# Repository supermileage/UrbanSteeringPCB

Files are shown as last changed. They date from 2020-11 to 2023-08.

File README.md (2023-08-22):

# Urban Steering PCB

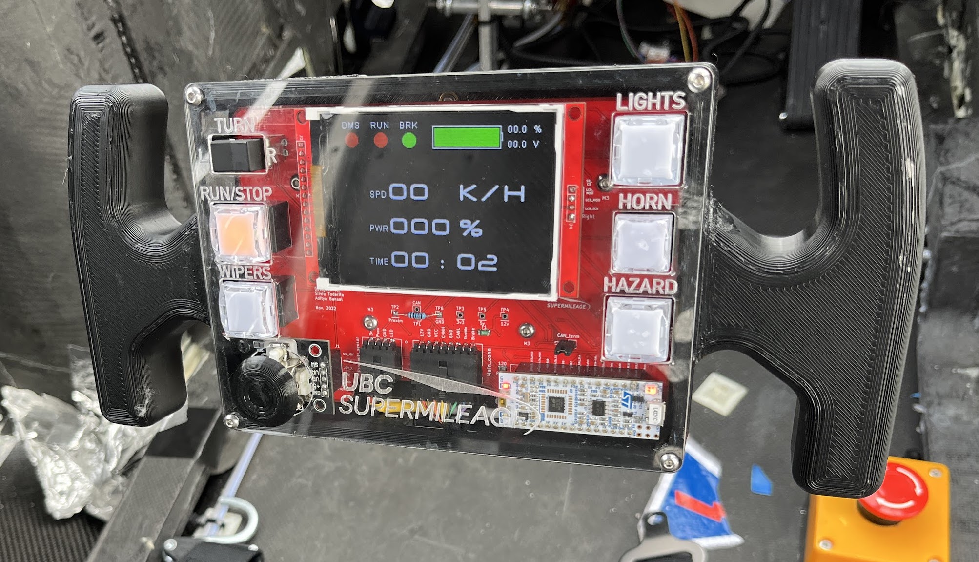
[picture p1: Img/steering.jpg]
Urban Steering Wheel


The steering wheel for the UBC Supermileage Urban Concept electric vehicle is designed to steer the vehicle, provide information to the driver, and allow the driver to control the vehicle. This repo contains the design files for the printed circuit board at the core of the steering wheel. 

Some features of this PCB:

- STM32L432 Microcontroller with built-in CAN controller
- MCP 2562 CAN Transceiver
- 74HC595 and 74HC597 shift registers for LED output & button input
- ILI9341 3.2" LCD Screen
- Mechanical buttons with dual-color LEDs
- IR proximity sensor for dead man's switch functionality
- SD Card Reader
- Joystick

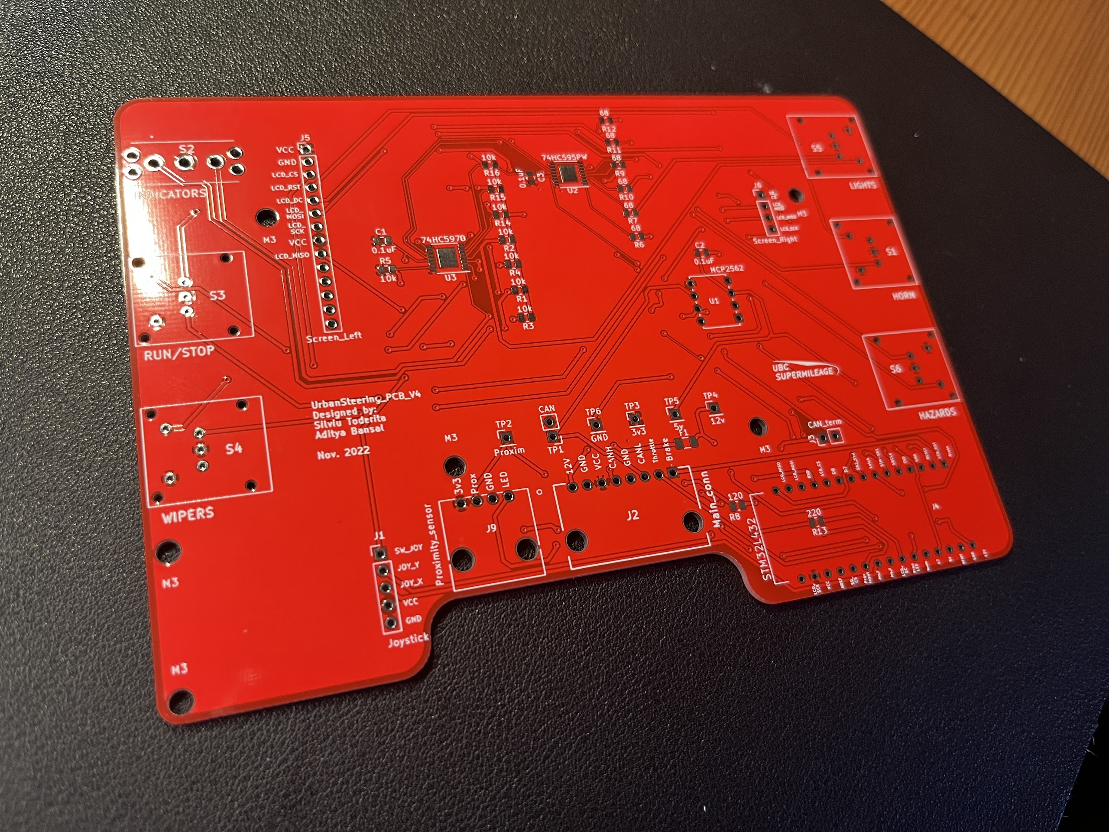
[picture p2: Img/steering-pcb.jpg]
Urban Steering PCB


## Schematic

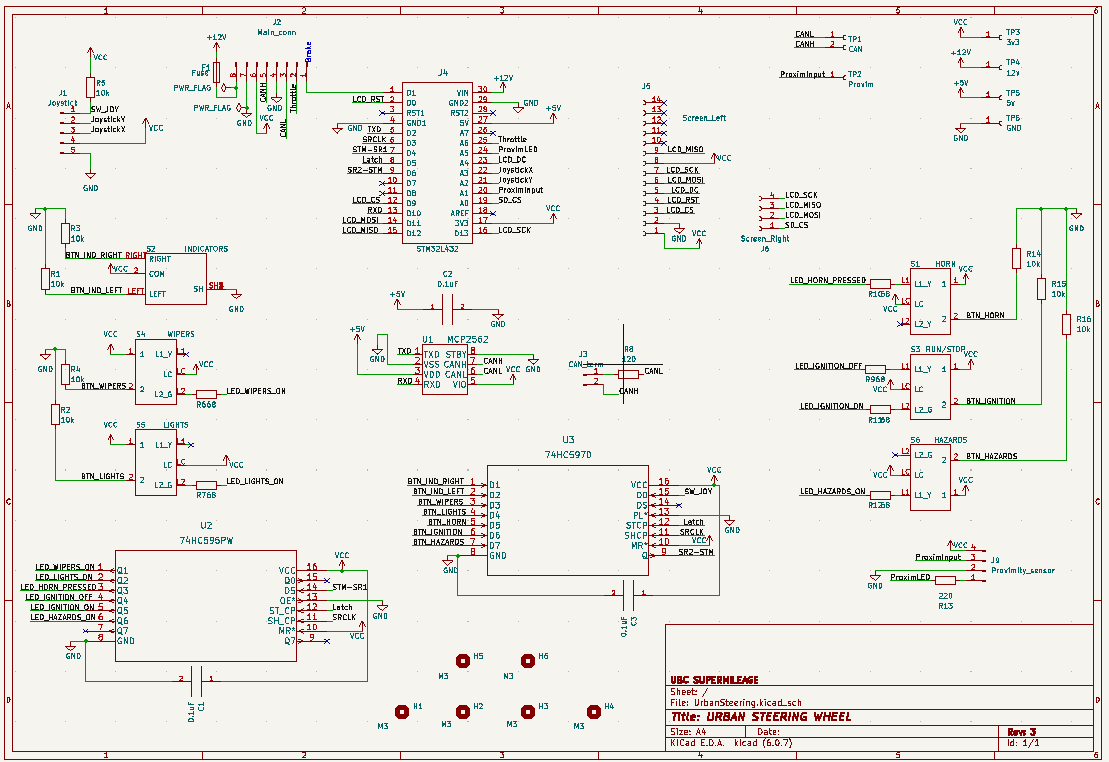
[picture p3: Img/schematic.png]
Schematic Diagram


## Layout 

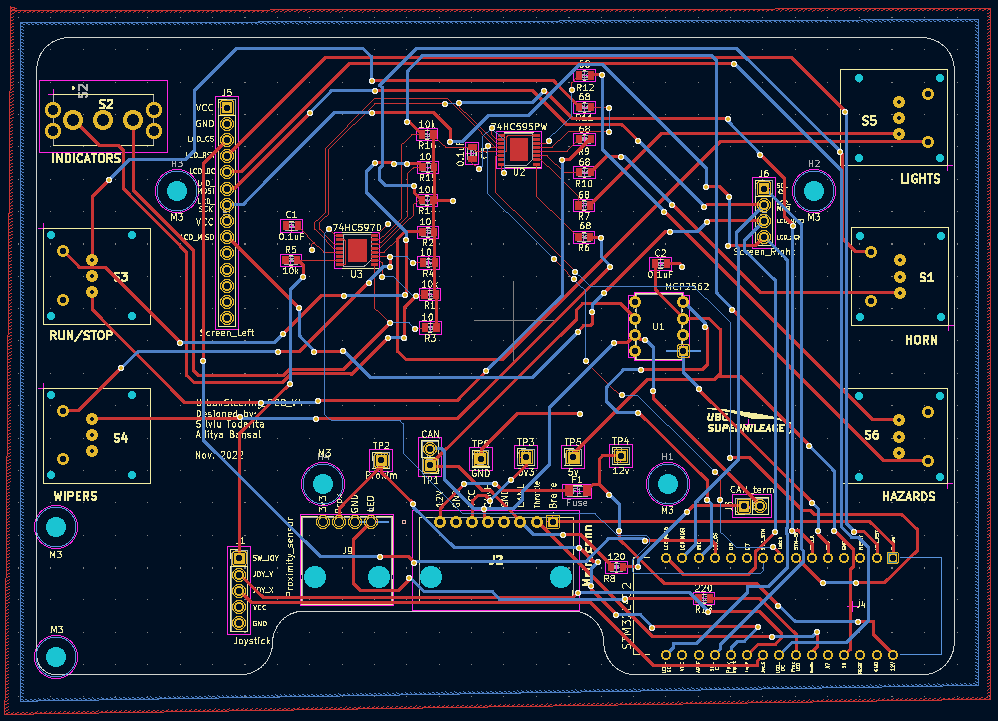
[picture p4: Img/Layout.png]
Unfilled Layout


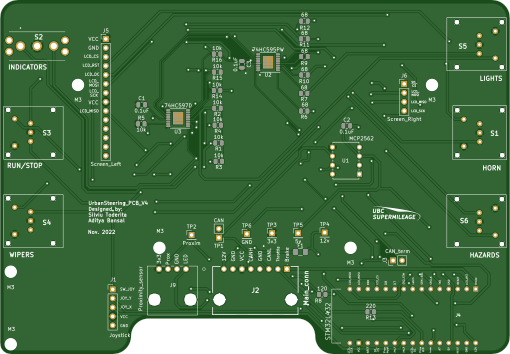
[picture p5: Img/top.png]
Front Render


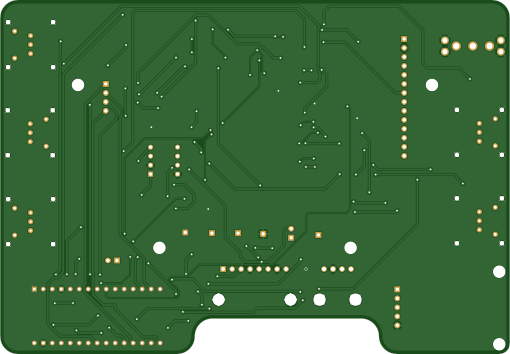
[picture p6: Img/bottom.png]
Back Render


## Bill of Materials
Found on [Notion](https://www.notion.so/Bill-of-Materials-6644a4c081e64de49a3c111644f56321)

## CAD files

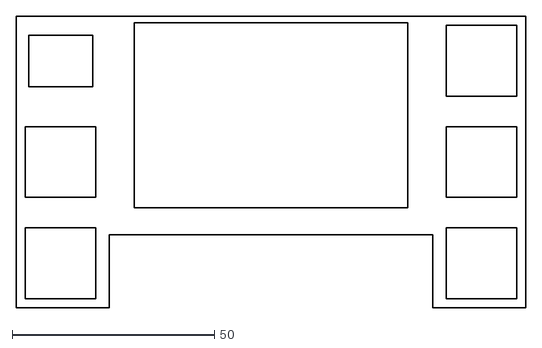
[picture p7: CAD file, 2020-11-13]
PCB Sketch V2.dxf
126.0 x 72.0

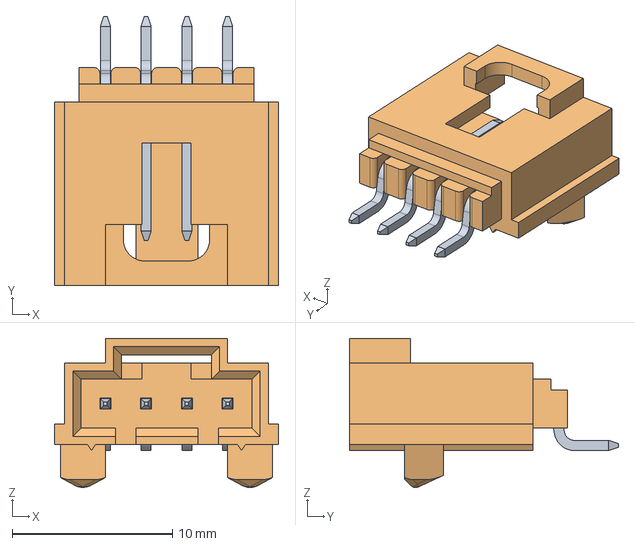
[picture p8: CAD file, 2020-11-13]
ProjectLibraries/Conn_Molex_15-91-2045/eec.models/Molex_-_15-91-2045.step
14.0 x 16.8 x 9.29 mm

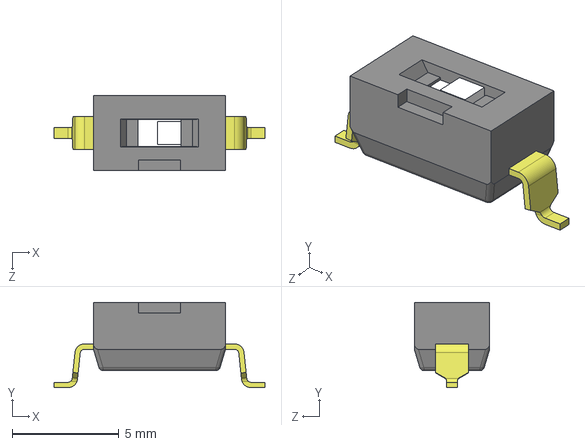
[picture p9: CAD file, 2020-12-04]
ProjectLibraries/dip_swtich_1pos/CUI_DEVICES_DS04-254-2-01BK-SMT.step
9.90 x 4.00 x 3.54 mm

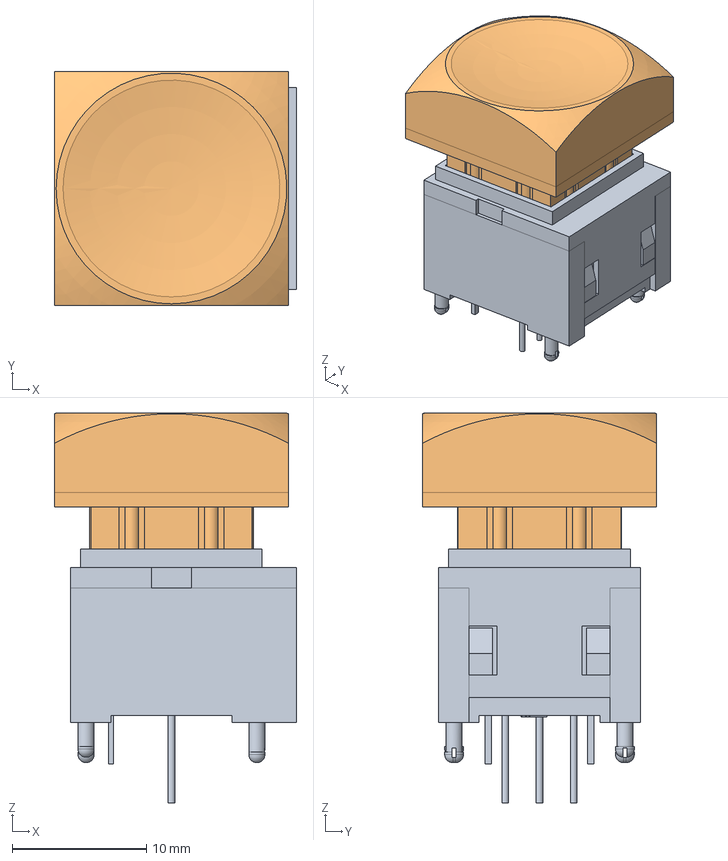
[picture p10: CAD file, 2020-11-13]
ProjectLibraries/LP11EE1NCSxx.stp
18.0 x 17.4 x 29.0 mm

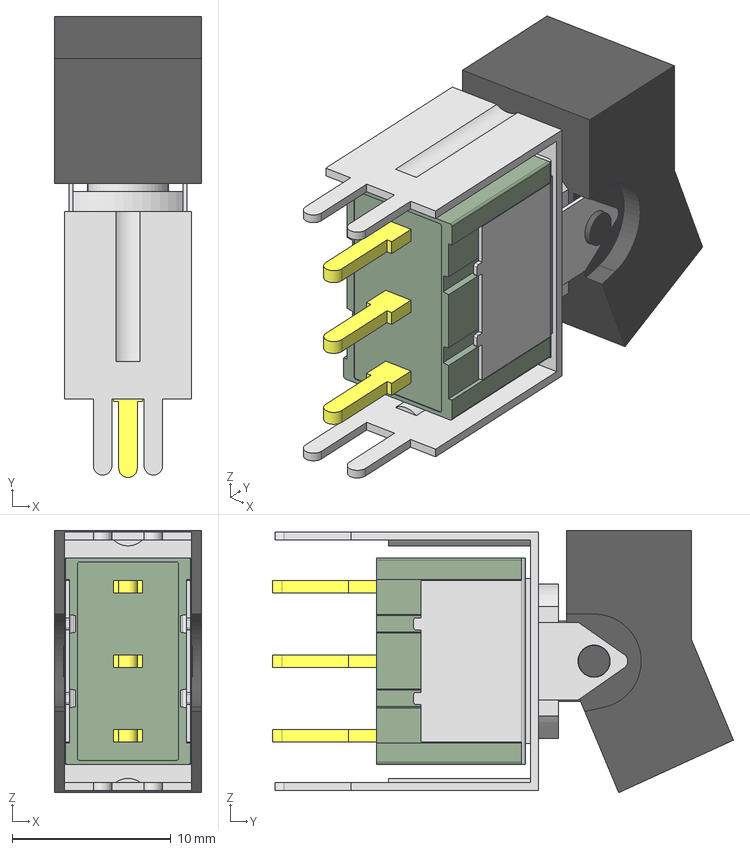
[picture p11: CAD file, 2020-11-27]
ProjectLibraries/Rocker_switch_M2022TXG13-DA/M2013TXG13-DA.stp
9.27 x 29.1 x 16.5 mm
_M201TX313-switch
_M201TX-cover
_M201TX13-cover-t
_BBracket-13TX-bracket
_AT4148-1A-rocker
_M201303GBR-terminal

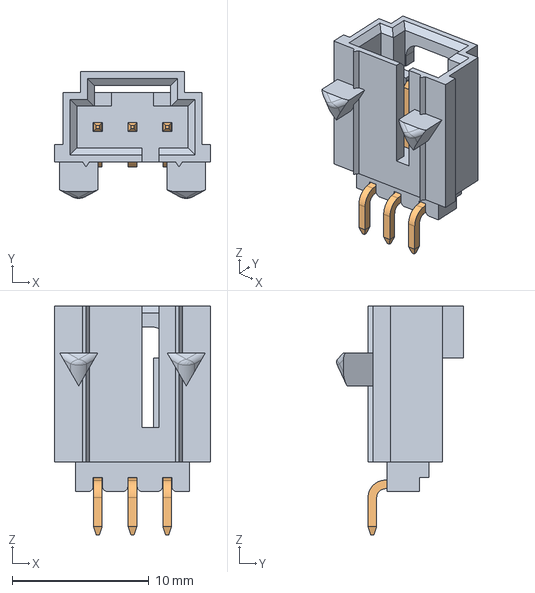
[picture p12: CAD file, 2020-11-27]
ProjectLibraries/15-91-2035/015912035.stp
11.4 x 9.29 x 16.8 mm

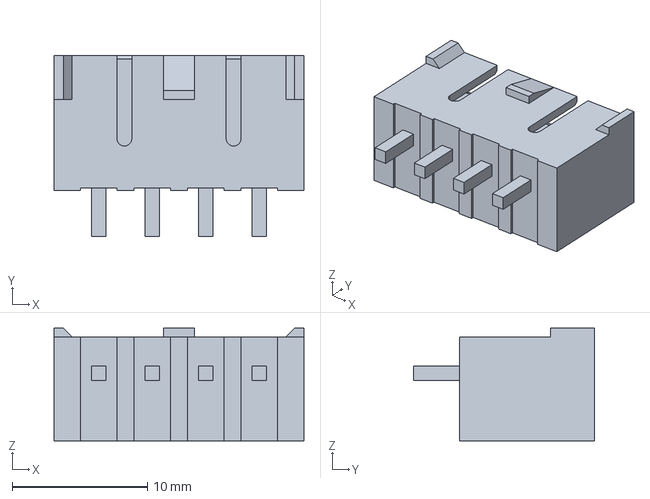
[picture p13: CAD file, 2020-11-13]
ProjectLibraries/35313-0460_step/353130460.stp
18.5 x 13.4 x 8.35 mm

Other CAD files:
ProjectLibraries/Conn_Molex_15-91-2045/015912045.stp

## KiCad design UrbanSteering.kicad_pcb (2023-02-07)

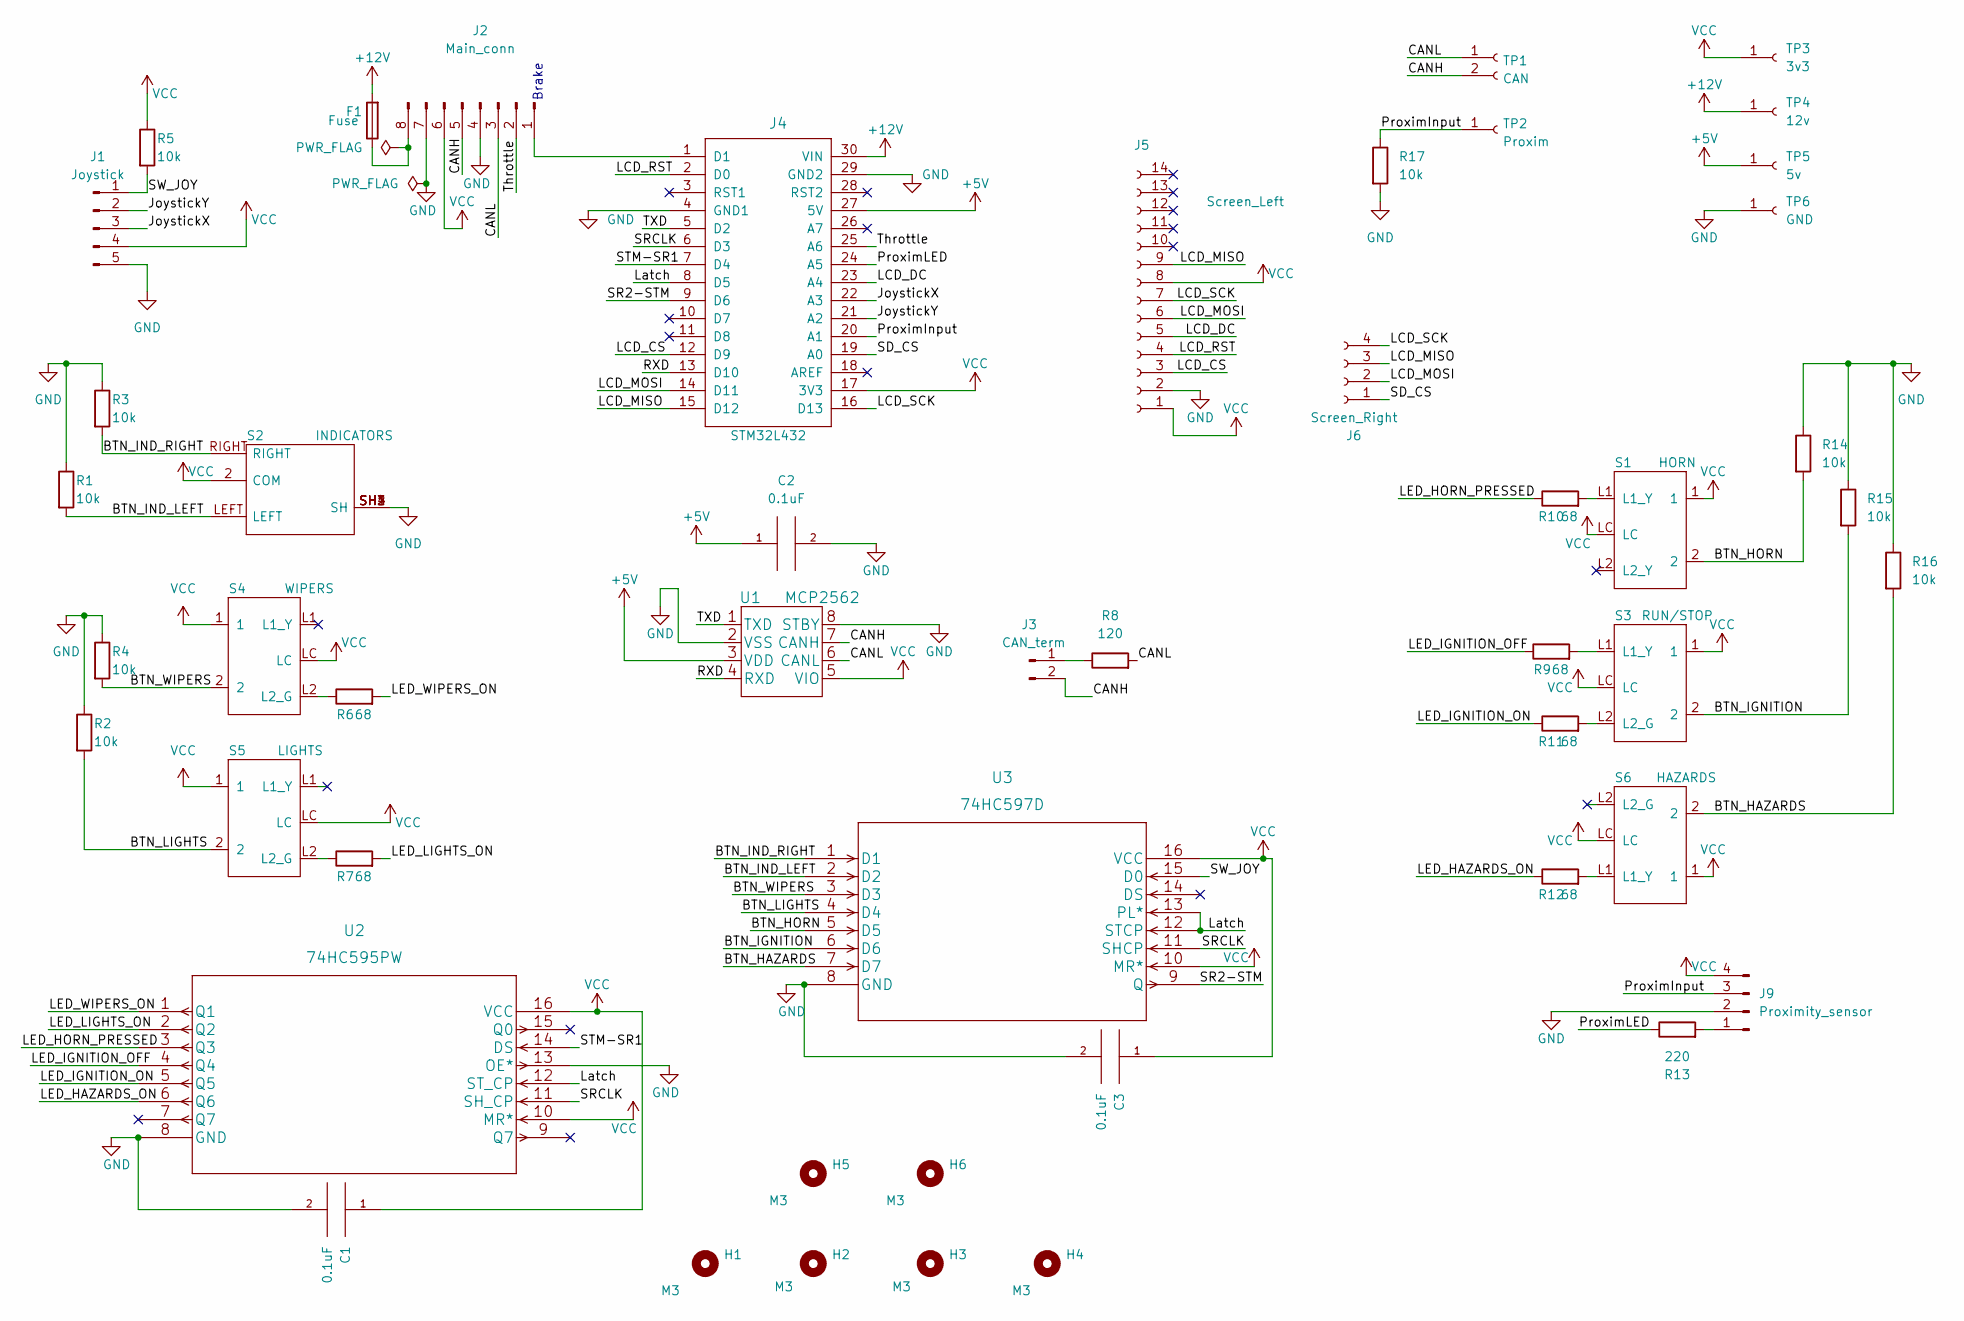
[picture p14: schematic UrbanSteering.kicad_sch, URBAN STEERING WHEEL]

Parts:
C1, C2, C3: 0.1uF; C_0805_2012Metric
F1: Fuse; Fuse_1206_3216Metric
H1, H2, H3, H4, H5, H6: M3; MountingHole_3.2mm_M3
J1: Joystick; PinHeader_1x05_P2.54mm_Vertical
J2: Main_conn; 705510007
J3: CAN_term; PinHeader_1x02_P2.54mm_Vertical
J4: STM32L432
J5: Screen_Left; PinHeader_1x14_P2.54mm_Vertical
J6: Screen_Right; PinHeader_1x04_P2.54mm_Vertical
J9: Proximity_sensor; 705510003
R1, R2, R3, R4, R5, R14, R15, R16, R17: 10k; R_0805_2012Metric
R6, R7, R9, R10, R11, R12: 68; R_0805_2012Metric
R8: 120; R_0805_2012Metric
R13: 220; R_0805_2012Metric
S1: HORN; LP11OA1TCSYY
S2: INDICATORS; M2013TXG13DA
S3: RUN/STOP; LP11EE1NCSYG
S4: WIPERS; LP11EE1NCSYG
S5: LIGHTS; LP11EE1NCSYG
S6: HAZARDS; LP11EE1NCSYG
TP1: CAN; PinHeader_1x02_P2.54mm_Vertical
TP2: Proxim; PinHeader_1x01_P2.54mm_Vertical
TP3: 3v3; PinHeader_1x01_P2.54mm_Vertical
TP4: 12v; PinHeader_1x01_P2.54mm_Vertical
TP5: 5v; PinHeader_1x01_P2.54mm_Vertical
TP6: GND; PinHeader_1x01_P2.54mm_Vertical
U1: MCP2562; MCP2562FD-H&slash_P
U2: 74HC595PW; TSSOP-16-1EP_4.4x5mm_P0.65mm
U3: 74HC597D; TSSOP-16-1EP_4.4x5mm_P0.65mm

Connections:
+5V: C2.1, J4.27 (5V), TP5.1, U1.3 (VDD)
+12V: F1.2, J4.30 (VIN), TP4.1
/BTN_HAZARDS: R16.2, S6.2, U3.7 (D7)
/BTN_HORN: R14.2, S1.2, U3.5 (D5)
/BTN_IGNITION: R15.2, S3.2, U3.6 (D6)
/BTN_IND_LEFT: R1.2, S2.LEFT, U3.2 (D2)
/BTN_IND_RIGHT: R3.2, S2.RIGHT, U3.1 (D1)
/BTN_LIGHTS: R2.2, S5.2, U3.4 (D4)
/BTN_WIPERS: R4.2, S4.2, U3.3 (D3)
/CANH: J2.5, J3.2, TP1.2, U1.7 (CANH)
/CANL: J2.3, R8.2, TP1.1, U1.6 (CANL)
/JoystickX: J1.3, J4.22 (A3)
/JoystickY: J1.2, J4.21 (A2)
/LCD_CS: J4.12 (D9), J5.3
/LCD_DC: J4.23 (A4), J5.5
/LCD_MISO: J4.15 (D12), J5.9, J6.3
/LCD_MOSI: J4.14 (D11), J5.6, J6.2
/LCD_RST: J4.2 (D0), J5.4
/LCD_SCK: J4.16 (D13), J5.7, J6.4
/LED_HAZARDS_ON: R12.1, U2.6 (Q6)
/LED_HORN_PRESSED: R10.1, U2.3 (Q3)
/LED_IGNITION_OFF: R9.1, U2.4 (Q4)
/LED_IGNITION_ON: R11.1, U2.5 (Q5)
/LED_LIGHTS_ON: R7.2, U2.2 (Q2)
/LED_WIPERS_ON: R6.2, U2.1 (Q1)
/Latch: J4.8 (D5), U2.12 (ST_CP), U3.12 (STCP), U3.13 (PL*)
/ProximInput: J4.20 (A1), J9.3, R17.1, TP2.1
/ProximLED: J4.24 (A5), R13.1
/RXD: J4.13 (D10), U1.4 (RXD)
/SD_CS: J4.19 (A0), J6.1
/SR2-STM: J4.9 (D6), U3.9 (Q)
/SRCLK: J4.6 (D3), U2.11 (SH_CP), U3.11 (SHCP)
/STM-SR1: J4.7 (D4), U2.14 (DS)
/SW_JOY: J1.1, R5.2, U3.15 (D0)
/TXD: J4.5 (D2), U1.1 (TXD)
/Throttle: J2.2, J4.25 (A6)
GND: C1.2, C2.2, C3.2, J1.5, J2.4, J2.7, J4.4 (GND1), J4.29 (GND2), J5.2, J9.2, R1.1, R2.1, R3.1, R4.1, R14.1, R15.1, R16.1, R17.2, S2.SH1 (SH), S2.SH2 (SH), S2.SH3 (SH), S2.SH4 (SH), TP6.1, U1.2 (VSS), U1.8 (STBY), U2.8 (GND), U2.13 (OE*), U3.8 (GND)
unnamed: F1.1, J2.8
unnamed: J2.1, J4.1 (D1)
unnamed: J3.1, R8.1
unnamed: J9.1, R13.2
unnamed: R6.1, S4.L2 (L2_G)
unnamed: R7.1, S5.L2 (L2_G)
unnamed: R9.2, S3.L1 (L1_Y)
unnamed: R10.2, S1.L1 (L1_Y)
unnamed: R11.2, S3.L2 (L2_G)
unnamed: R12.2, S6.L1 (L1_Y)
VCC: C1.1, C3.1, J1.4, J2.6, J4.17 (3V3), J5.1, J5.8, J9.4, R5.1, S1.1, S1.LC, S2.2 (COM), S3.1, S3.LC, S4.1, S4.LC, S5.1, S5.LC, S6.1, S6.LC, TP3.1, U1.5 (VIO), U2.10 (MR*), U2.16 (VCC), U3.10 (MR*), U3.16 (VCC)

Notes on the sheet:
Brake

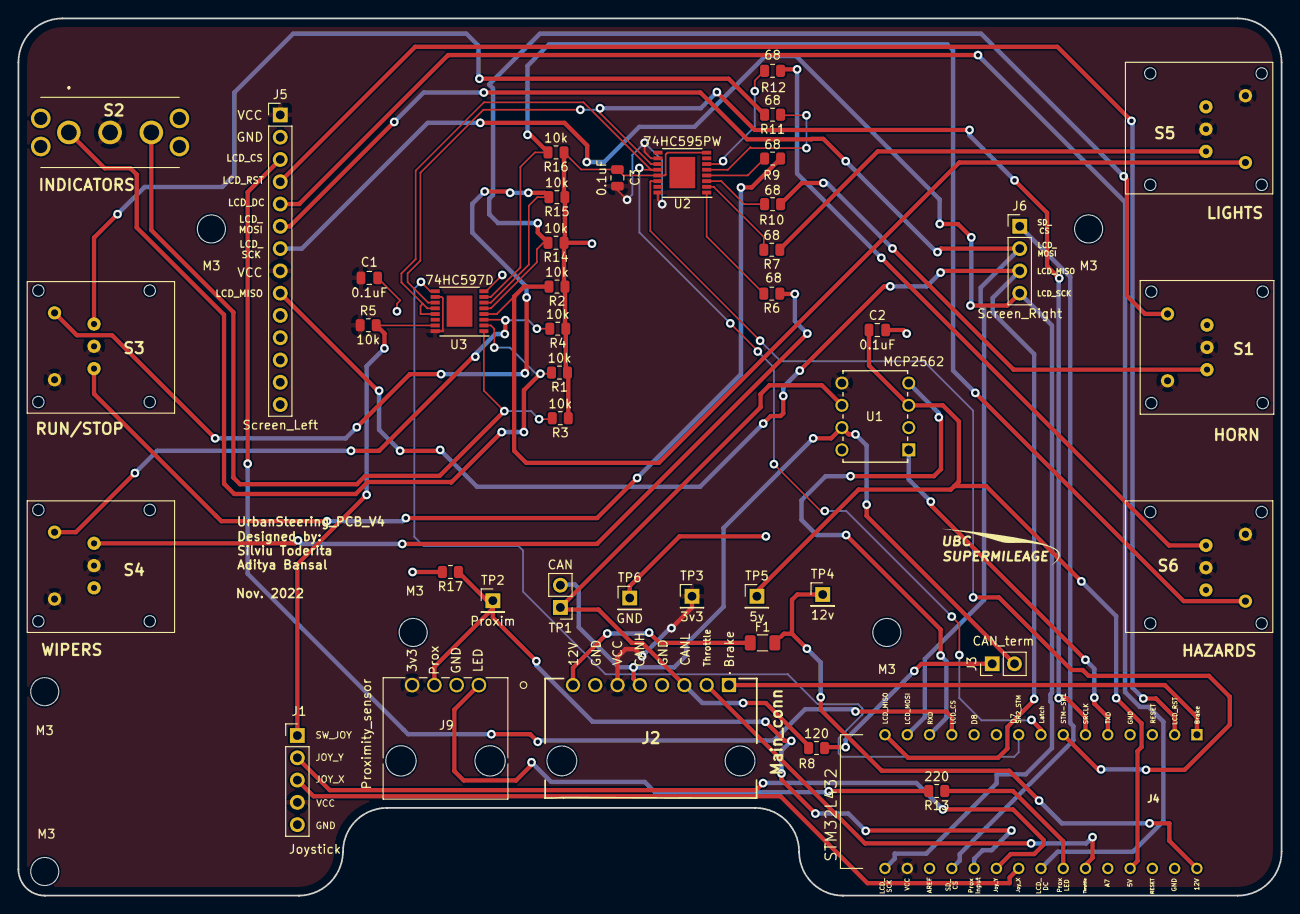
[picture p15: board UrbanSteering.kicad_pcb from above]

Board: 2 copper layers, 144.0 x 100.0 mm, 50 parts (0 on the bottom side), 48 nets.

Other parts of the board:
SUPERMILEAGE: LOGO; Logo_bitmap

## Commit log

2020-11-27 ALMOST DONE, ROUTING LEFT
    [015912035.stp, 015912045.stp, LP11EE1NCSxx.stp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]
2020-12-04 V3 done design review pending
    [CUI_DEVICES_DS04-254-2-01BK-SMT.step, schematic.kicad_pcb, schematic.sch]
2020-12-08 EVERYTHING COMPLETE POST DESIGN REVIEW
    [schematic.kicad_pcb, schematic.sch]
2021-01-04 Cleaned up labels and fixed DRC warnings
    [schematic.kicad_pcb, schematic.sch]
2021-01-04 Cleaned file structure
    [015912035.stp, 015912045.stp, 353130460.stp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]
2021-01-05 Cleaned up project structure, schematic and mask. Changed the DC connection for the TFT
    [015912035.stp, 015912045.stp, 353130460.stp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]
2021-01-10 Generated fab files
    [BOM.xlsx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]
2021-01-20 Cleaned up, added to readme, added images, new outputs
    [UrbanSteering-B_Mask.gbs, UrbanSteering-B_Paste.gbp, UrbanSteering-B_SilkS.gbo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]
2021-01-20 Removed old files
    [UrbanSteering.kicad_pcb]
2022-10-23 added components and started wiring
    [UrbanSteering.kicad_sch]
2022-11-03 PCB version 4
    [UrbanSteering.kicad_sch]
2022-11-05 PCB version-4 with mounting holes
    [UrbanSteering.kicad_sch, UrbanSteering.sch]
2022-11-05 started pcb layout
    [UrbanSteering.kicad_pcb, UrbanSteering.kicad_sch]
2022-11-07 PCB version-4 layout 1.0
    [UrbanSteering.kicad_pcb]
2022-11-07 PCB version 4 layout 2.0
    [UrbanSteering.kicad_pcb]
2022-11-07 PCB version 4 layout 3.0
    [UrbanSteering.kicad_pcb]
2022-11-07 adjusts position of some footprints, adds most required labels, deletes existing traces, flips LCD orientation, and adjusts netclass sizes
    [BOM.xlsx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]
2022-11-07 makes bottom filled zone GND and adds some connections from top SMD component grounds
    [UrbanSteering.kicad_pcb]
2022-11-09 added top filled zone for VCC
    [UrbanSteering.kicad_pcb]
2022-11-09 added labels and tracing... Some errors on DRC
    [UrbanSteering.kicad_pcb]
2022-11-10 updated clearance settings and connected some non-contiguous filled zones
    [UrbanSteering.kicad_pcb]
2022-11-10 added label names on STM
    [UrbanSteering.kicad_pcb]
2022-11-26 added fuse to schematic - layout to be changed
    [UrbanSteering.kicad_pcb, UrbanSteering.kicad_sch]
2022-11-27 added labels
    [UrbanSteering.kicad_pcb, UrbanSteering.kicad_sch]
2022-11-29 made capacitor and stm shifting change, also edited main connector labels
    [UrbanSteering.kicad_pcb]
2022-11-30 made all changes
    [UrbanSteering.kicad_pcb]
2022-12-01 adds output files
    [UrbanSteering-B_Mask.gbs, UrbanSteering-B_Paste.gbp, UrbanSteering-B_Silkscreen.gbo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]
2022-12-03 added images
    [UrbanSteering-B_Mask.gbs, UrbanSteering-B_Paste.gbp, UrbanSteering-B_Silkscreen.gbo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]
2023-02-06 Physical hardware changes replicated in KiCad design
    [UrbanSteering.kicad_pcb, UrbanSteering.kicad_sch]

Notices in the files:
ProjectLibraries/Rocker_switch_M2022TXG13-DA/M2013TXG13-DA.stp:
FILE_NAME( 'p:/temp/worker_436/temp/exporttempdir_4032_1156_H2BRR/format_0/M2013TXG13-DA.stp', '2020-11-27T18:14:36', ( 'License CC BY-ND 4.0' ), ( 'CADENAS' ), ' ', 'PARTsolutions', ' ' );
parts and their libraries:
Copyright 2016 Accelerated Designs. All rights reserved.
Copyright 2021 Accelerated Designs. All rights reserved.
